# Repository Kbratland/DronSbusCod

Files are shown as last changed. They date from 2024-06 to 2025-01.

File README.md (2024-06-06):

header
<details>  
    <summary>
        <b>Description of XV-Swarm-24</b>
    </summary>
    <p>The objective of this class was to create and program swarm drones ourselves. For the first few weeks of class, we worked on building the drones using a parts kit. To legally fly the drone, we needed approval for multiple FAA and school district waivers, some of which had to be revised. We also created the necessary code from scratch, including the keyboard and flex stick controls, the communications from the Arduino to the flight controller, the access point, and the base station.</p>
</details>

<details> 
    <summary>
        <b>Regulatory Compliance</b>
    </summary>

    - FAA Multi Waiver
    - RSD Multi Waiver
    - § 107.35 – Operation of Multiple Small UAS
    - Register With FAA
    - Register RSD with ODA
    - Request Fria 

</details>

<details>
    <summary>
        <h3>Drone Building Instructions and Parts List</h3>
    </summary>
    <details>
        <summary>
            <b>Frame Construction</b>
        </summary>
        <a href="https://github.com/Kbratland/DronSbusCod/blob/main/Instructions/FrameConstruction.md">Frame Instructions</a>
    </details>
    <details>
        <summary>
            <b>Wiring!</b>
        </summary>
        <a href="https://github.com/Kbratland/DronSbusCod/blob/main/Instructions/Wiring.md">Wiring Instructions</a>
    </details>
    <details>
        <summary>
            <b>Code installation and Configuration</b>
        </summary>
            <details>
                <summary>
                       Code
                </summary>
             <a href="https://github.com/Kbratland/DronSbusCod/blob/main/Instructions/CodeInstall.md">Code Installation Instructions</a>
            </details>
            <details>
                <summary>
                    Configuration
                </summary>
                <a href="https://github.com/Kbratland/DronSbusCod/blob/main/Instructions/Configuration.md">Configuration Instructions</a>
            </details>
    </details>
    <details>
        <summary>
            <b>Parts Needed:</b>
        </summary>
        -<a href="https://www.digikey.com/en/products/detail/jst-sales-america-inc/A08SR08SR30K203A/9922207">8-Pin JST Cable </a> <br>
        -<a href="https://holybro.com/collections/autopilot-flight-controllers/products/kakute-f4-v2-4">Kakute F4 v2.4 Flight Controller</a> <br>
        -<a href="https://holybro.com/collections/motors/products/ripper-1404-3800kv-ultralight-brushless-motor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">Ripper Motor Four-pack</a> <br>
        -<a href="https://www.amazon.com/1500mAh-Graphene-Quadcopter-Helicopter-Airplane/dp/B09CTS2KY6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">Ovonic Lipo Battery</a> <br>
        -<a href="https://holybro.com/collections/autopilot-peripherals/products/tekko32-f4-4in1-mini-50a-esc">Tekko-32 Motor Controller</a> <br>
        -<a href="https://holybro.com/collections/power-modules-pdbs/products/pm02-v3-12s-power-module">Battery Cable Adapter</a> <br>
        -<a href="https://holybro.com/collections/standard-gps-module/products/micro-m10-m9n-gps">Micro M10 GPS</a> <br>
        -<a href="https://betafpv.com/products/hq-3030-2-blade-propellers-1-5-shaft-16-pcs?variant=29700573528108">16x 3-Blade Propellers</a> <br>
        -<a href="https://store-usa.arduino.cc/products/arduino-nano-33-iot">Arduino Nano 33 IOT</a> <br>
        -<a href="https://store.arduino.cc/products/nodemcu-esp8266">NodeMCU ESP8266</a>, subject to change <br>
        <br><p>Screw and insert types below, feel free to use different than the link provides</p>
        -<a href="https://www.amazon.com/gp/product/B07TTQXVQH/ref=ox_sc_act_title_1?smid=A19TVI3M6WFVG7&th=1">M1.6 Brass Screw Insert</a> <br>
        -<a href="https://www.amazon.com/M1-6x4mm-0-35mm-Pitch-Socket-100pcs/dp/B00XP4ZWY2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">M1.6 .35mm Screw</a> <br>
        -<a href="https://www.amazon.com/initeq-M3-0-5-Threaded-Inserts-Printing/dp/B077CJV3Z9?th=1">M3 Brass Screw Insert</a> <br>
        -<a href="https://www.amazon.com/Socket-Screws-Bolts-Thread-100pcs/dp/B07CNFTK99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">M3 12mm Screw</a> <br>
    </details>
</details>

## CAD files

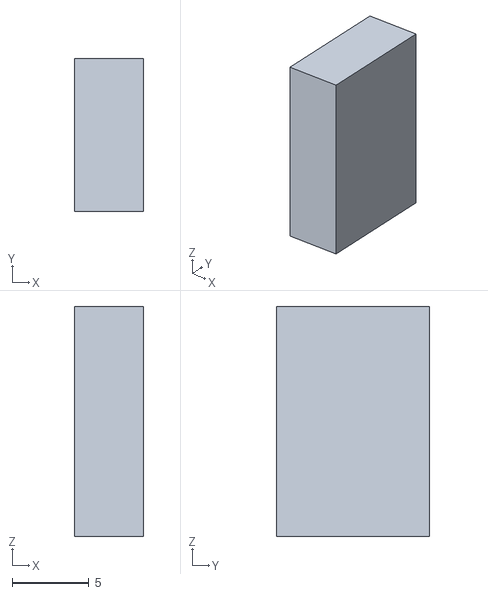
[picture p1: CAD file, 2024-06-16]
Drone CAD Files/Key x2.stl
4.50 x 10.0 x 15.0

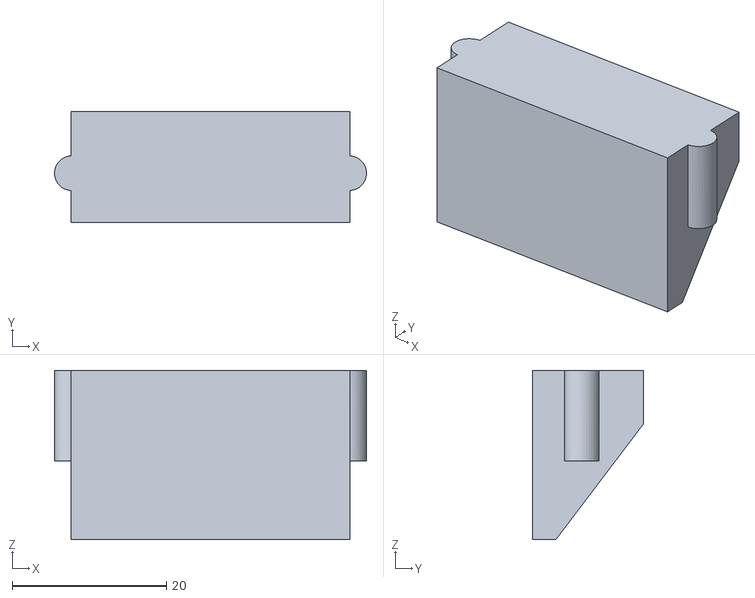
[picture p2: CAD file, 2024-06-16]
Drone CAD Files/Holder.stl
40.5 x 14.4 x 22.0

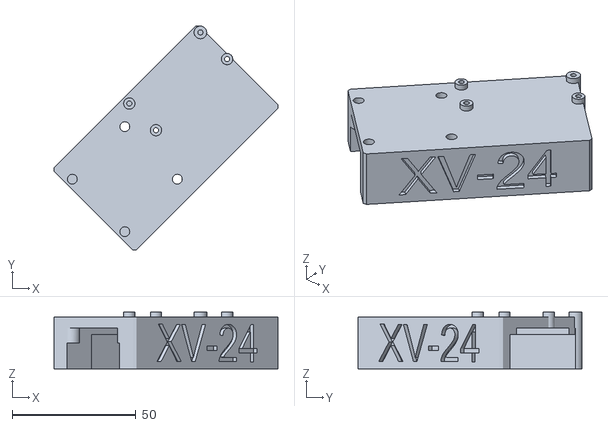
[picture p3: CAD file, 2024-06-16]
Drone CAD Files/Harness.stl
90.5 x 90.5 x 23.0

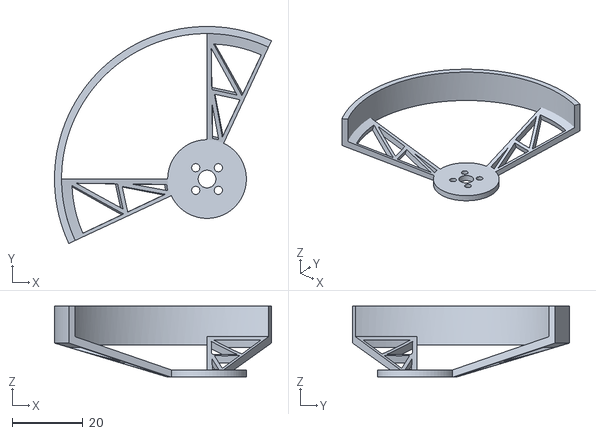
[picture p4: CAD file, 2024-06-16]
Drone CAD Files/Prop Protector x4.stl
61.2 x 61.2 x 20.0

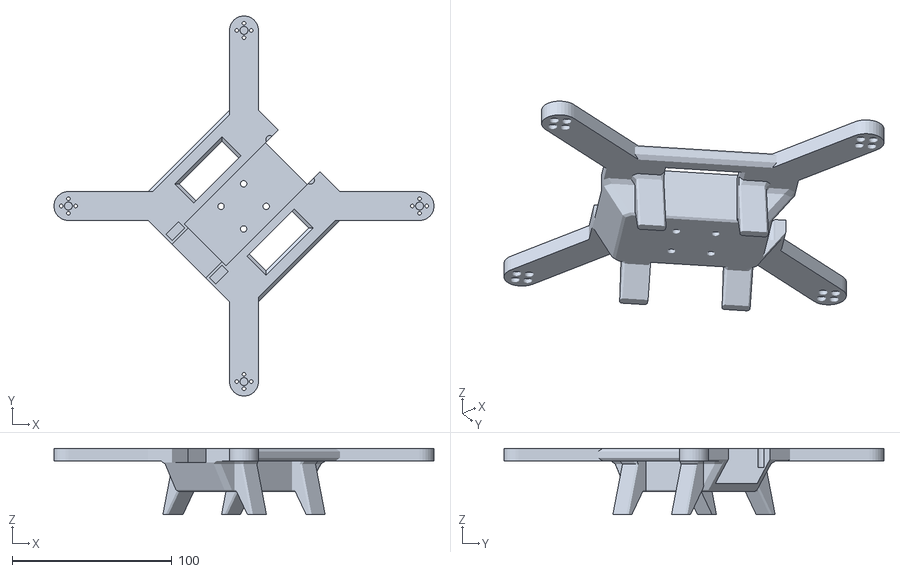
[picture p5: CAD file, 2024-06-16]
Drone CAD Files/Drone Frame.stl
238.1 x 238.1 x 41.7

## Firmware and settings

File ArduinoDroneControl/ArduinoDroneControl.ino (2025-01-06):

#include <WiFiNINA.h>                    //https://github.com/arduino-libraries/WiFiNINA/tree/master
#include <WiFiUDP.h>                     
#include <sbus.h>                        //https://github.com/bolderflight/SBUS

char ssid[] = "XV_Basestation";          //  network SSID (name)
int status = WL_IDLE_STATUS;             // the Wi-Fi radio's status
int ledState = LOW;                      //ledState used to set the LED
unsigned long previousMillisInfo = 0;    //will store last time Wi-Fi information was updated
unsigned long previousMillisLED = 0;     // will store the last time LED was updated
const int intervalInfo = 5000;           // interval at which to update the board information
char packetBuffer[256];                  //buffer to hold incoming packet
WiFiUDP Udp;
unsigned int localPort = 2390;
char  ReplyBuffer[] = "Drone 1";
int wifiState = 0;                       //Wifi connection state
bool firstConnectFrame = false;          //First Loop while connected to wifi
double pytime = 0;                        //time of python code

bool serialUSB = false;
 
//KONERRRRRR
/* SBUS object, writing SBUS */
bfs::SbusTx sbus_tx(&Serial1);
/* SBUS data */
bfs::SbusData data;

double pitch; // pitch is broken?
double roll;
double yaw;
double throttle;
int arming;
int updateTime = 0;
int connectTime = 0;
long t = 0;
bool isArmed = false;
bool isFailsafed = false;
bool isKilled = false;
long blinkTime = 0;
int droneState = -1;  
int killswitch = 1000;
int failsafe = 1000;
int LEDpin = 13;
int blinkSpeed = 10;
bool lightOn = false;
bool bootComplete = false;               //Finished Drone Booting sequence
bool enabled = false;

//KOOONNNEEER
IPAddress bsip; //holds the base station ip address

struct ManualControlMessage{
  IPAddress sourceIP;
  String cmd;
  double yaw;
  double pitch;
  double roll;
  double throttle;
  double killswitch;
  double pytime;
};

struct BSIPMessage{
  String cmd;
  IPAddress BSIP;
};

void setup() {
  //Initialize serial and wait for port to open:
  Serial.begin(115200);
  if(Serial)
  {
    serialUSB = true;
    Serial.println("Setup");
  }
  delay(1000);
  DataSetSend();
  delay(1000);
  // set the LED as output
  pinMode(LED_BUILTIN, OUTPUT);
  sbus_tx.Begin();
  roll = 1500;
  pitch = 1500;
  yaw = 1500;
  throttle = 885;
  WifiConnection();
}//end setup

void loop() {
  status = WiFi.status();
//   if(status != WL_CONNECTED)
//   {  
//     blinkSpeed = 50;
//     failsafe = 2000;
//   }
//   else
//   {
//     failsafe = 1000;
//   }
  //MillisStuff();
  WifiConnection();//checks the wi-fi status
  Listen();
  DroneSystems();
  DataSetSend();
  if (wifiState == 1 && droneState == 1 && status == WL_CONNECTED){
    Udp.beginPacket(Udp.remoteIP(), Udp.remotePort());
    Udp.write("State: 1 -> 2");
    Udp.endPacket();
    wifiState = 2;
  }
  else if (wifiState == 2){ 
    Udp.beginPacket(Udp.remoteIP(), Udp.remotePort());
    Udp.write("AmDrone");
    Udp.endPacket();
    wifiState = 3;
  }
  else if (wifiState == 4) {
    Udp.beginPacket(bsip, 5005);
    Udp.write("HND|-1|NEWDRONE");
    Udp.endPacket();
    wifiState = 5; 
  }
  if(millis() - updateTime > 5000 && serialUSB)
  {
    Serial.println("<--------------------------->\nDrone Data");
    Serial.print("Throttle: "); Serial.println(throttle);
    Serial.print("Pitch: "); Serial.println(pitch);
    Serial.print("Roll: "); Serial.println(roll);
    Serial.print("Yaw: "); Serial.println(yaw);
    Serial.print("Armed: "); Serial.println(isArmed);
    Serial.print("Failsafe: "); Serial.println(isFailsafed);
    Serial.print("Killswitch: "); Serial.println(isKilled);
    Serial.println("<--------------------------->");
    updateTime = millis();
  }
  // else if (state == 5) {
  //   //call parsemanualcontrolmessage and process the results
  //   //but do it in listen
  //   // Serial.println(roll);
  //   // Serial.println(yaw);
  //   // Serial.println(pitch);
  //   // Serial.println(throttle);
  // }
}//End Loop

void DroneSystems(){
  if (droneState == -1){//starting up
    blinkSpeed = 1000;       
    throttle = 885;
    Arm(false);     
    if(millis() - t > 1000){
      t = millis();
      droneState = 0;
    }
  }
  else if (droneState == 0){//arm drone
    blinkSpeed = 1000;
    //set arming signals
    Arm(true);
    if (millis() - t > 500){
      droneState = 1;
      t = millis();
    }
  }
  else if (droneState == 1) //nothing
  {
    //Roll Ch 0, pitch Ch 1, Yaw Ch 3, Throttle Ch 2, Arm Ch 4
    
  }
  else if(droneState == 2)
  {
    
    
  }
  if(status != WL_CONNECTED) 
  {
    if(millis()- blinkTime >= blinkSpeed){
      LightSRLatch();
      blinkTime = millis();
    }
  }
  else if(droneState == -1 || droneState == 0){ //Light Blinker
    if(millis()- blinkTime >= blinkSpeed){
      LightSRLatch();
      blinkTime = millis();
    }
  }
  else if(killswitch == 1700){
    digitalWrite(LEDpin,LOW);
  }
  else{
    digitalWrite(LEDpin,HIGH);
  }
  CheckModeStates();
  // delay(10);  
}//End Drone Systems

void Arm(bool armed)
{
  if(armed)
  {
    arming = 2000;
  }
  else if(!armed)
  {
    arming = 1000;
  }
}

void CheckModeStates(){ //sets booleans of the modes for enabled/disabled
  if(arming > 1500)
  {
    isArmed = true;
  }
  else
  {
    isArmed = false;
  }
  if(failsafe > 1500)
  {
    isFailsafed = true;
  }
  else
  {
    isFailsafed = false;
  }
  if(killswitch > 1500)
  {
    isKilled = true;
  }
  else
  {
    isKilled = false;
  }
}

int ChannelMath(double setpoint) //Math to set the same values as used in inav veiwer, < 0.0001% stray
{
  //channel limits assume setpoint between 900 - 2100
  setpoint = (setpoint - 879.7)/.6251;
  return round(setpoint);  
}

void LightSRLatch()
{
  if(lightOn)
  {
    digitalWrite(LEDpin, LOW);
    lightOn = false;    
  }
  else if(!lightOn)
  {
    digitalWrite(LEDpin, HIGH);
    lightOn = true;    
  }
}

void WifiConnection()
{
  // attempt to connect to Wi-Fi network:
  if(status != WL_CONNECTED && ((millis() - connectTime) > 5000)) {
    if(serialUSB)
    {
      Serial.print("Attempting to connect to network: ");
    }
    Serial.println(ssid);
    // Connect to WPA/WPA2 network:
    status = WiFi.begin(ssid);
    //Retry every 5 seconds
    firstConnectFrame = true;
    connectTime = millis();
  }
  else if(status == WL_CONNECTED && firstConnectFrame)
  {
    Udp.begin(localPort);
      // Udp.beginPacket(Udp.remoteIP(), Udp.remotePort());
    Udp.beginPacket("192.168.4.22", 80);
    Udp.write("State: 0 -> 1 |Connected|");
    Udp.endPacket();
    wifiState = 1;
    
    Udp.beginPacket("192.168.4.22", 80);
    Udp.write(ReplyBuffer);
    Udp.endPacket();
    // you're connected now, so print out the data:
    if(serialUSB)
    {
      printBoardInfo();
    }
    firstConnectFrame = false;
    bootComplete = true;
  }
}

void DataSetSend() //Sends data over sbus
{
  data.ch[0] = (ChannelMath(roll));
  data.ch[1] = (ChannelMath(pitch)); 
  data.ch[2] = (ChannelMath(throttle));
  data.ch[3] = (ChannelMath(yaw));
  data.ch[4] = (ChannelMath(arming));
  data.ch[5] = (ChannelMath(1500));
  data.ch[6] = (ChannelMath(1500));
  data.ch[7] = (ChannelMath(failsafe));
  data.ch[8] = (ChannelMath(1500));
  data.ch[9] = (ChannelMath(1500));
  data.ch[10] = (ChannelMath(2000));
  data.ch[11] = (ChannelMath(1500)); //RSSI (Signal Strenght)
  data.ch[12] = (ChannelMath(killswitch)); //Killswitch
  data.ch[13] = (ChannelMath(1500));
  data.ch[14] = (ChannelMath(1500));
  data.ch[15] = (ChannelMath(1500));
  sbus_tx.data(data);
  sbus_tx.Write();
}

void SendMessage(char msg[]){
  Udp.begin(localPort);
  // Udp.beginPacket(Udp.remoteIP(), Udp.remotePort());
  Udp.beginPacket("192.168.4.22", 80);
  Udp.write(msg);
  Udp.endPacket();
  Serial.println("Sent");
  Serial.println(msg);
  Serial.println("**********");
}

void printBoardInfo(){
  Serial.println("Board Information:");
  // print your board's IP address:
  IPAddress ip = WiFi.localIP();
  Serial.print("IP Address: ");
  Serial.println(ip);

  // print your network's SSID:
  Serial.println();
  Serial.println("Network Information:");
  Serial.print("SSID: ");
  Serial.println(WiFi.SSID());

  // print the received signal strength:
  long rssi = WiFi.RSSI();
  Serial.print("signal strength (RSSI):");
  Serial.println(rssi);
  Serial.println("---------------------------------------");
  Serial.println("You're connected to the network");
  Serial.println("---------------------------------------");

}

void MillisStuff() { //specifies whatever this stuff is for use in the loop, to make the looop easier to read
  unsigned long currentMillisInfo = millis();

  // check if the time after the last update is bigger the interval
  if (currentMillisInfo - previousMillisInfo >= intervalInfo) {
    previousMillisInfo = currentMillisInfo;

  }
  
  unsigned long currentMillisLED = millis();
  
  // measure the signal strength and convert it into a time interval
  int intervalLED = WiFi.RSSI() * -10;
 
  // check if the time after the last blink is bigger the interval 
  if (currentMillisLED - previousMillisLED >= intervalLED) {
    previousMillisLED = currentMillisLED;

    // if the LED is off turn it on and vice-versa:
    if (ledState == LOW) {
      ledState = HIGH;
    } else {
      ledState = LOW;
    }

    // set the LED with the ledState of the variable:
    digitalWrite(LED_BUILTIN, ledState);
  }
}

ManualControlMessage parseMessage(char buffer[]){
  ManualControlMessage msg;
  char *token;
  token = strtok(buffer, "|");
  int i = 0;
  while(token != 0){
    //Serial.println(token);
    switch(i){
      case 0:
        msg.cmd = token;
        break;
      case 1:
        msg.sourceIP = token;
        break;
      case 2:
        msg.yaw = atoi(token);       
        break;
      case 3:
        msg.pitch = atoi(token);  //pitch
        break;
      case 4: 
        msg.roll = atoi(token);
        break;
      case 5:
        msg.throttle = atoi(token);
        break;
      case 6:
        msg.killswitch = atoi(token);
        break;
      case 7:
        msg.pytime = atoi(token);
        break;
      }
      roll = msg.roll;
      pitch = msg.pitch;
      throttle = msg.throttle;
      yaw = msg.yaw;
      killswitch = msg.killswitch;
      pytime = msg.pytime;
    i++;
    token = strtok(NULL, "|"); 
  }
return msg;  
//HAS REQUIRED PACKETS FROM LISTEN, CODE FOR MANUAL MODE HERE --------------
//Currently does not include a break, repeats loop forever
}  

BSIPMessage parseBSIP(char buffer[]){
  BSIPMessage msg;
  char *token;
  token = strtok(buffer, "|");
  int i = 0;
  Serial.println("In parseBSIP");
  while(token != 0){
    Serial.println(token);
    switch(i){
      case 0:
        msg.cmd = token;
        break;
      case 1:
        msg.BSIP = token;
        break;        
      }
    i++;
    token = strtok(NULL, "|");
    
  }
  return msg;  
}  

void Listen(){
  int packetSize = Udp.parsePacket();
  if(packetSize){
    //Serial.print("Received packet of size ");
    //Serial.println(packetSize);
    //Serial.print("From ");
    IPAddress remoteIp = Udp.remoteIP();
    //Serial.print(remoteIp);
    //Serial.print(", port ");
    //Serial.println(Udp.remotePort());
    // read the packet into packetBufffer
    int len = Udp.read(packetBuffer, 255);
    //Serial.println(packetBuffer);
    if (len > 0) {
      packetBuffer[len] = 0;
      if (wifiState == 3){
        Serial.println("Parsing BSIP Message");
        //read BSID response from AP      
        BSIPMessage msg = parseBSIP(packetBuffer);
        if (msg.cmd == "BSIP"){
          bsip = msg.BSIP;
          Serial.print("Base Station IP: ");
          Serial.println(bsip);
          wifiState = 4;
        }
      }
      else if (wifiState == 5){
        //Serial.println("listening for manual message");
        ManualControlMessage msg = parseMessage(packetBuffer);
        if(serialUSB)
        {
          Serial.print("packet: ");
          Serial.print(msg.throttle);
          Serial.print(" recived at: ");
          Serial.print(millis());
        }
        if (msg.cmd == "MAN"){
          roll = msg.roll;
          pitch = msg.pitch;
          throttle = msg.throttle;
          yaw = msg.yaw;
          DataSetSend();
        }
      }
    }    
  }
}
=======
#include <WiFiNINA.h>                    //https://github.com/arduino-libraries/WiFiNINA/tree/master
#include <WiFiUDP.h>                     
#include <sbus.h>                        //https://github.com/bolderflight/SBUS

char ssid[] = "XV_Basestation";          //  network SSID (name)
int status = WL_IDLE_STATUS;             // the Wi-Fi radio's status
int ledState = LOW;                      //ledState used to set the LED
unsigned long previousMillisInfo = 0;    //will store last time Wi-Fi information was updated
unsigned long previousMillisLED = 0;     // will store the last time LED was updated
const int intervalInfo = 5000;           // interval at which to update the board information
char packetBuffer[256];                  //buffer to hold incoming packet
WiFiUDP Udp;
unsigned int localPort = 2390;
char  ReplyBuffer[] = "Drone 1";
int wifiState = 0;                       //Wifi connection state
bool firstConnectFrame = false;          //First Loop while connected to wifi
double pytime = 0;                        //time of python code

bool serialUSB = false;
 
//KONERRRRRR
/* SBUS object, writing SBUS */
bfs::SbusTx sbus_tx(&Serial1);
/* SBUS data */
bfs::SbusData data;

double pitch; // pitch is broken?
double roll;
double yaw;
double throttle;
int arming;
int updateTime = 0;
int connectTime = 0;
long t = 0;
bool isArmed = false;
bool isFailsafed = false;
bool isKilled = false;
long blinkTime = 0;
int droneState = -1;  
int killswitch = 1000;
int failsafe = 1000;
int LEDpin = 13;
int blinkSpeed = 10;
bool lightOn = false;
bool bootComplete = false;               //Finished Drone Booting sequence
bool enabled = false;

//KOOONNNEEER
IPAddress bsip; //holds the base station ip address

struct ManualControlMessage{
  IPAddress sourceIP;
  String cmd;
  double yaw;
  double pitch;
  double roll;
  double throttle;
  double killswitch;
  double pytime;
};

struct BSIPMessage{
  String cmd;
  IPAddress BSIP;
};

void setup() {
  //Initialize serial and wait for port to open:
  Serial.begin(115200);
  if(Serial)
  {
    serialUSB = true;
    Serial.println("Setup");
  }
  delay(1000);
  DataSetSend();
  delay(1000);
  // set the LED as output
  pinMode(LED_BUILTIN, OUTPUT);
  sbus_tx.Begin();
  roll = 1500;
  pitch = 1500;
  yaw = 1500;
  throttle = 885;
  WifiConnection();
}//end setup

void loop() {
  status = WiFi.status();
  if(status != WL_CONNECTED)
  {  
    blinkSpeed = 50;
    failsafe = 2000;
  }
  else
  {
    failsafe = 1000;
  }
  //MillisStuff();
  WifiConnection();//checks the wi-fi status
  Listen();
  DroneSystems();
  DataSetSend();
  if (wifiState == 1 && droneState == 1 && status == WL_CONNECTED){
    Udp.beginPacket(Udp.remoteIP(), Udp.remotePort());
    Udp.write("State: 1 -> 2");
    Udp.endPacket();
    wifiState = 2;
  }
  else if (wifiState == 2){ 
    Udp.beginPacket(Udp.remoteIP(), Udp.remotePort());
    Udp.write("AmDrone");
    Udp.endPacket();
    wifiState = 3;
  }
  else if (wifiState == 4) {
    Udp.beginPacket(bsip, 5005);
    Udp.write("HND|-1|NEWDRONE");
    Udp.endPacket();
    wifiState = 5; 
  }
  if(millis() - updateTime > 5000 && serialUSB)
  {
    Serial.println("<--------------------------->\nDrone Data");
    Serial.print("Throttle: "); Serial.println(throttle);
    Serial.print("Pitch: "); Serial.println(pitch);
    Serial.print("Roll: "); Serial.println(roll);
    Serial.print("Yaw: "); Serial.println(yaw);
    Serial.print("Armed: "); Serial.println(isArmed);
    Serial.print("Failsafe: "); Serial.println(isFailsafed);
    Serial.print("Killswitch: "); Serial.println(isKilled);
    Serial.println("<--------------------------->");
    updateTime = millis();
  }
  // else if (state == 5) {
  //   //call parsemanualcontrolmessage and process the results
  //   //but do it in listen
  //   // Serial.println(roll);
  //   // Serial.println(yaw);
  //   // Serial.println(pitch);
  //   // Serial.println(throttle);
  // }
}//End Loop

void DroneSystems(){
  if (droneState == -1){//starting up
    blinkSpeed = 1000;       
    throttle = 885;
    Arm(false);     
    if(millis() - t > 1000){
      t = millis();
      droneState = 0;
    }
  }
  else if (droneState == 0){//arm drone
    blinkSpeed = 1000;
    //set arming signals
    Arm(true);
    if (millis() - t > 500){
      droneState = 1;
      t = millis();
    }
  }
  else if (droneState == 1) //nothing
  {
    //Roll Ch 0, pitch Ch 1, Yaw Ch 3, Throttle Ch 2, Arm Ch 4
    
  }
  else if(droneState == 2)
  {
    
    
  }
  if(status != WL_CONNECTED) 
  {
    if(millis()- blinkTime >= blinkSpeed){
      LightSRLatch();
      blinkTime = millis();
    }
  }
  else if(droneState == -1 || droneState == 0){ //Light Blinker
    if(millis()- blinkTime >= blinkSpeed){
      LightSRLatch();
      blinkTime = millis();
    }
  }
  else if(killswitch == 1700){
    digitalWrite(LEDpin,LOW);
  }
  else{
    digitalWrite(LEDpin,HIGH);
  }
  CheckModeStates();
  // delay(10);  
}//End Drone Systems

void Arm(bool armed)
{
  if(armed)
  {
    arming = 2000;
  }
  else if(!armed)
  {
    arming = 1000;
  }
}

void CheckModeStates(){ //sets booleans of the modes for enabled/disabled
  if(arming > 1500)
  {
    isArmed = true;
  }
  else
  {
    isArmed = false;
  }
  if(failsafe > 1500)
  {
    isFailsafed = true;
  }
  else
  {
    isFailsafed = false;
  }
  if(killswitch > 1500)
  {
    isKilled = true;
  }
  else
  {
    isKilled = false;
  }
}

int ChannelMath(double setpoint) //Math to set the same values as used in inav veiwer, < 0.0001% stray
{
  //channel limits assume setpoint between 900 - 2100
  setpoint = (setpoint - 879.7)/.6251;
  return round(setpoint);  
}

void LightSRLatch()
{
  if(lightOn)
  {
    digitalWrite(LEDpin, LOW);
    lightOn = false;    
  }
  else if(!lightOn)
  {
    digitalWrite(LEDpin, HIGH);
    lightOn = true;    
  }
}

void WifiConnection()
{
  // attempt to connect to Wi-Fi network:
  if(status != WL_CONNECTED && ((millis() - connectTime) > 5000)) {
    if(serialUSB)
    {
      Serial.print("Attempting to connect to network: ");
    }
    Serial.println(ssid);
    // Connect to WPA/WPA2 network:
    status = WiFi.begin(ssid);
    //Retry every 5 seconds
    firstConnectFrame = true;
    connectTime = millis();
  }
  else if(status == WL_CONNECTED && firstConnectFrame)
  {
    Udp.begin(localPort);
      // Udp.beginPacket(Udp.remoteIP(), Udp.remotePort());
    Udp.beginPacket("192.168.4.22", 80);
    Udp.write("State: 0 -> 1 |Connected|");
    Udp.endPacket();
    wifiState = 1;
    
    Udp.beginPacket("192.168.4.22", 80);
    Udp.write(ReplyBuffer);
    Udp.endPacket();
    // you're connected now, so print out the data:
    if(serialUSB)
    {
      printBoardInfo();
    }
    firstConnectFrame = false;
    bootComplete = true;
  }
}

void DataSetSend() //Sends data over sbus
{
  data.ch[0] = (ChannelMath(roll));
  data.ch[1] = (ChannelMath(pitch)); 
  data.ch[2] = (ChannelMath(throttle));
  data.ch[3] = (ChannelMath(yaw));
  data.ch[4] = (ChannelMath(arming));
  data.ch[5] = (ChannelMath(1500));
  data.ch[6] = (ChannelMath(1500));
  data.ch[7] = (ChannelMath(failsafe));
  data.ch[8] = (ChannelMath(1500));
  data.ch[9] = (ChannelMath(1500));
  data.ch[10] = (ChannelMath(2000));
  data.ch[11] = (ChannelMath(1500)); //RSSI (Signal Strenght)
  data.ch[12] = (ChannelMath(killswitch)); //Killswitch
  data.ch[13] = (ChannelMath(1500));
  data.ch[14] = (ChannelMath(1500));
  data.ch[15] = (ChannelMath(1500));
  sbus_tx.data(data);
  sbus_tx.Write();
}

void SendMessage(char msg[]){
  Udp.begin(localPort);
  // Udp.beginPacket(Udp.remoteIP(), Udp.remotePort());
  Udp.beginPacket("192.168.4.22", 80);
  Udp.write(msg);
  Udp.endPacket();
  Serial.println("Sent");
  Serial.println(msg);
  Serial.println("**********");
}

void printBoardInfo(){
  Serial.println("Board Information:");
  // print your board's IP address:
  IPAddress ip = WiFi.localIP();
  Serial.print("IP Address: ");
  Serial.println(ip);

  // print your network's SSID:
  Serial.println();
  Serial.println("Network Information:");
  Serial.print("SSID: ");
  Serial.println(WiFi.SSID());

  // print the received signal strength:
  long rssi = WiFi.RSSI();
  Serial.print("signal strength (RSSI):");
  Serial.println(rssi);
  Serial.println("---------------------------------------");
  Serial.println("You're connected to the network");
  Serial.println("---------------------------------------");

}

void MillisStuff() { //specifies whatever this stuff is for use in the loop, to make the looop easier to read
  unsigned long currentMillisInfo = millis();

  // check if the time after the last update is bigger the interval
  if (currentMillisInfo - previousMillisInfo >= intervalInfo) {
    previousMillisInfo = currentMillisInfo;

  }
  
  unsigned long currentMillisLED = millis();
  
  // measure the signal strength and convert it into a time interval
  int intervalLED = WiFi.RSSI() * -10;
 
  // check if the time after the last blink is bigger the interval 
  if (currentMillisLED - previousMillisLED >= intervalLED) {
    previousMillisLED = currentMillisLED;

    // if the LED is off turn it on and vice-versa:
    if (ledState == LOW) {
      ledState = HIGH;
    } else {
      ledState = LOW;
    }

    // set the LED with the ledState of the variable:
    digitalWrite(LED_BUILTIN, ledState);
  }
}
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

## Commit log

2024-06-06 prints packet throttle at time recived
2024-06-06 Drone Stl and fusion files
    [Alignment Key2x.stl, Frame.stl, Harness.stl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]
2024-06-06 Cad Folder
    [Alignment Key2x.stl, Frame.stl, Harness.stl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]
2024-06-07 gets current time from python
2024-06-07 optimizeing, removing printing without serial usb
2024-06-16 Updated CAD
    [Alignment Key2x.stl, Drone Frame.stl, Frame.stl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]
